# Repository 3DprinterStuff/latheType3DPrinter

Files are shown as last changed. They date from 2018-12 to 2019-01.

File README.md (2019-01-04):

# latheType3DPrinter

this is a dump of files related to mod to convert a standard 3D-Printer to a lathe type 3D-printer. A lathe type printer prints on rolls, as described in https://de.scribd.com/doc/147351838/Lathe-Type-3D-Printer. Printing on a bottle was shown at the 35C3 (assembly only).

# contact me

you can reach me by mail: printerstuff@riseup.net

# hardware

The basis for the modifaction is a ANET A8 printer. This printer was used, because i expected to destroy the hardware while experimenting (so this is no recomendation). Luckily the hardware still lives.

The main modification was to remove the heatbead and to replace it with a roll.

## removing the heatbed

The heatbed can be removed the basicaly doing the build process in reverse. The heatbed, the gliders and the rod holding the heatbed were removed. To not confuse the 3Dprinter, the heatbed was put next to the 3Dprinter with the wirering still attached. It may server as a tea warmer from now on.

## choose a roll

Choose a sturdy and round rod or pipe to print on. The usual rules for surfaces apply. For PLA i found that paper rolls and a steel pipe covered in masking tape worked well. Bottles are fun, but not easy to work with. This is because the fillament (PLA) doesn't stick well on cold metal/glass. Putting masking tape or smearing a layer of glue on the roll helps with the adhesion. 

The roll should be as round as possible. Bottles are actually not round and paper rolls are often ovals, too. For carpet rolls plastic parts exist that ensure roundness and have centered holes that can be usefull for mounting. For metal pipes ensure a clean cut so the pipe doesn't wobble later. A properly manufactured roll would probably best.

## mounting the roll

build some sort of contraption that holds the roll in place while rotating. The contraption must allow the bottle to rotate on the Y axis.

The rotational axis should be below the extruder to ensure the printing is happening on top of the bottle instead of on the side of the bottle. Printing a bit on the side of the roll causes little harm, but is bad style.

The rotational axis has to be parallel to the printers X axis. If the rotational axis is missalined printing quality will suffer or the print will fail, since the distance between the roll and the extruder won't be uniform. 

This can be validated by positioning the extruder ~ 1 mm above the roll and moving the Y/X Axis. If the distance to the roll stays uniform, the roll is mounted perfectly.

In this repo there are mountpoints that can be clicked into the case of an ANET A8 and multiple holders for different rolls. These holders are very custom (exept for the mate bottle one). The designs are very simple so you probably want to design your own. If you are printing

The bearings for the mounts in this repo are engines from old harddrives (HDD). Using standardised bearings would be the smarter thing probably, but costs hacker points.

## make the roll roll

Many 3D printers have the mechanics for X/Z Axis on top and the side of the printer and move the heatbead to have an Y Axis. The roll should replace the headbed and transform horizontal Y Axis movement with rotational Y Axis movement. This transformation happens by moving the upper part of a toothwheel instead of the heatbed. 

The toothwheel should be fitted onto the roll in a way it doesn't slip. In the best case it is easy to remove, centered and is tight enough to not rotate around the roll.

The orginal timing belt was cut and bolted onto the heatbed. A new and looped timing belt should be aquired and placed so it connects the Y Axis enigine with the upper side of the toothwheel. The timing belt should fit tight to reduce chances of skipping and to improve precision. In my case i used the wheel opposite of the Y Axis engine, but with some more distance than usual. 

The timing belt i used was from an old scanner so the dimension of your timing belt will likely differ. You should ensure it has roughly the needed length and take care it has the proper distance between the teeth. In my case it was 2 mm distance between the teeth. My guess is that for historical reasons any timing belts removed from old scanners will work.

## using the mechanics

With the modification done the 3D-printer should be ready to work. You can test the basic motion by doing the movement manually. If the printer doesn't fall apart and the roll stays centered below the extruder for multiple complete rotations, the mechanics should be fine.

One issue to resolve is how to handle the z-stopper. The usual position will probably way too low, so i removed it and press it manually when needed. As an unpleasent side effect is that the extruder will ram into the roll until the button is pressed or something. Since the button will never be pressed something will break so be carefull. This is especially bad, if the gcode for a print contains a HOME Z or HOME X/Y/Z for example at the start or the end of the print.

## homing the printer

The X-axis can be homed like without a modification. I prefer moving the X-axis to a point 1-2 cm left of the start of the roll and reset the printer. This is very dirty, but works for me. Feel free to solve this properly though.

The Y-Axis doesn't have to be homed at all, if the roll is has no special sides. Homing the Y-Axis will still result in the roll rotating till the y-stopper is pressed manually. This results in a fast rotation, but the roll and the rolls mount should be able to handle it.

I home the Z-Axis by moving the extruder above the roll and triggering the HOME-Z manually. The printer does a fast movent first where you should stop the extruder ~ 1 mm above the roll. Press the Z-stopper once to stop the extruder. Immediatly afterwards the printer will move the extruder up a bit and solwer it slowly again. Press the Z-stopper again to stop the extruder ~ 0.2 mm above the roll.

The printer should be homed now. I disabled/removed automatic homing in the gcode to prevent accidential destruction of the device. Also the printer should be prevented from moving throuh the holders for the roll when done with the printing.

## actually print something

You may print aribtrary 3D models that were sliced traditionally. Since the printers Firmware and slices behaves as the roll is a long flatbed it will print but will have of perspective skew. for some millimeter high the skew is negligeble for objects that are some centimeters high the skew will be obvious. The printer will also have a maximum value for the y coordiniate. This will have to be disabled or circumvented. In my printers case nagative Y coordinates were not capped and moving to -40000 mm Y was possible.

I prefered to write g-code generators in python. This allowed my to do what i actually want to do. While the sourcecode is in this repository it is very bad code and not abstracted properly.

An proper slicer or a more abstracted gcode generator is future work amound other things.

## what now ?

For the moment i'll glady help anybody to convert 3D printers to rotation based 3D printers. Also i welcome any energy put towards to having a slicer or an abstracted gcode generator for this type of printer. Please talk to me though, so we have the opportunity to coordinate.

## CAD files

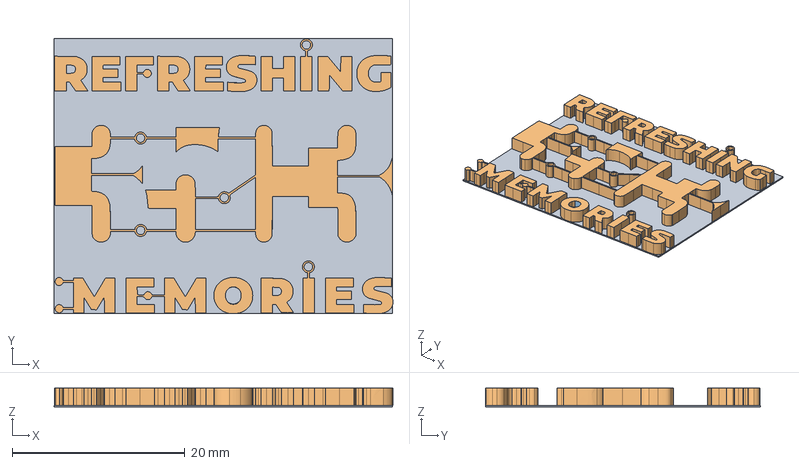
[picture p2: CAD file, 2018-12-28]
5Dprinter/35c3_logo_try6.fcstd
39.3 x 31.9 x 2.20 mm
Scale001
Pad001Body

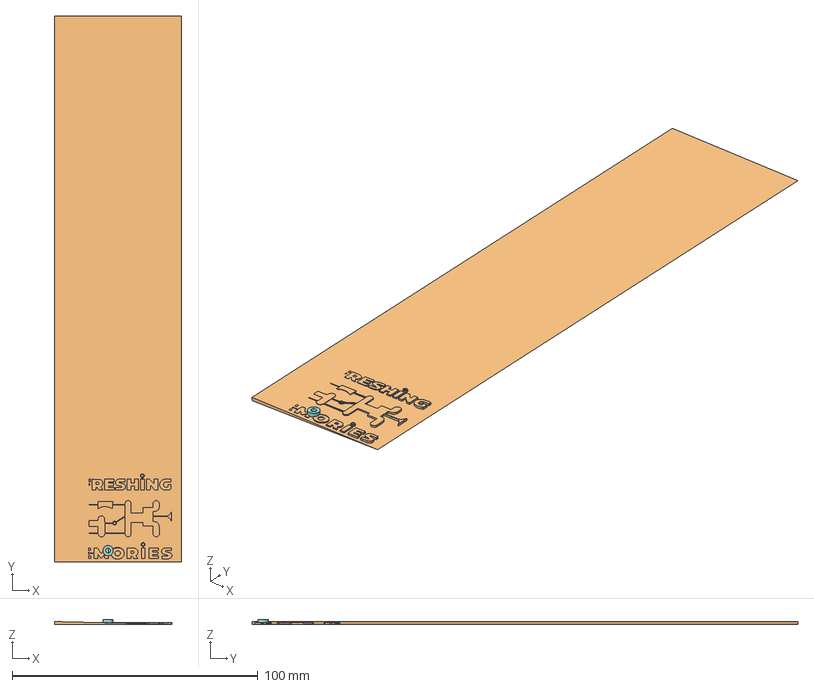
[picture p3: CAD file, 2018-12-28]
5Dprinter/bottle_print/logo_splited_5.fcstd
51.8 x 222.0 x 2.10 mm
Pad001Body
Scale004
PadBody
PocketBody
Pad001Body001
Pad002Body
Scale005

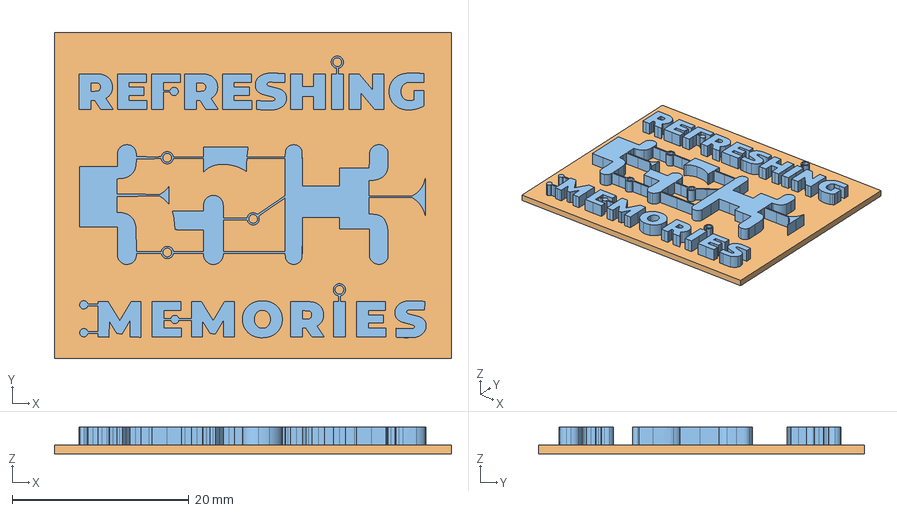
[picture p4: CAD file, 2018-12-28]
5Dprinter/35c3_logo_try3.fcstd
44.9 x 36.9 x 3.00 mm
Scale001

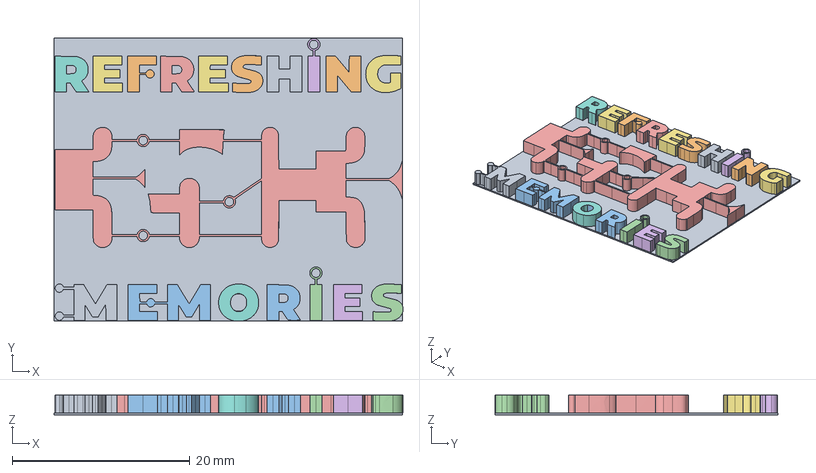
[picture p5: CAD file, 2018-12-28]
5Dprinter/35c3logo_6_2.stp
39.3 x 31.9 x 2.20 mm

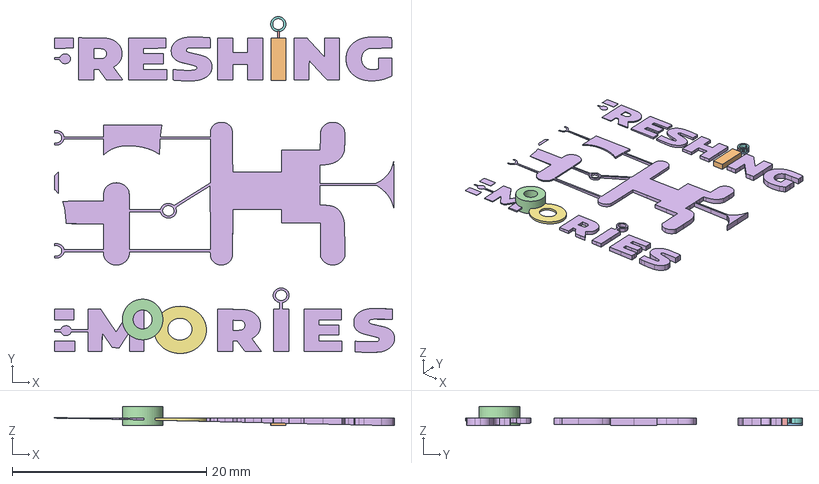
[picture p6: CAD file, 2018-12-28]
5Dprinter/bottle_print/logo_upper.fcstd
35.0 x 34.7 x 2.00 mm
Pad001Body
PadBody
PocketBody
Pad001Body001
Pad002Body

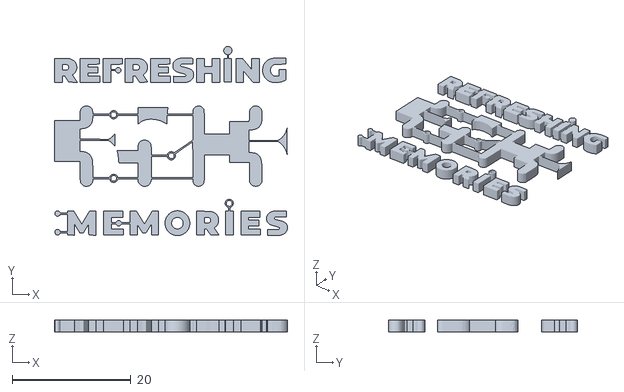
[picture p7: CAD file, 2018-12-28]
5Dprinter/35c3_logo1_txt.stl
39.2 x 31.8 x 2.00

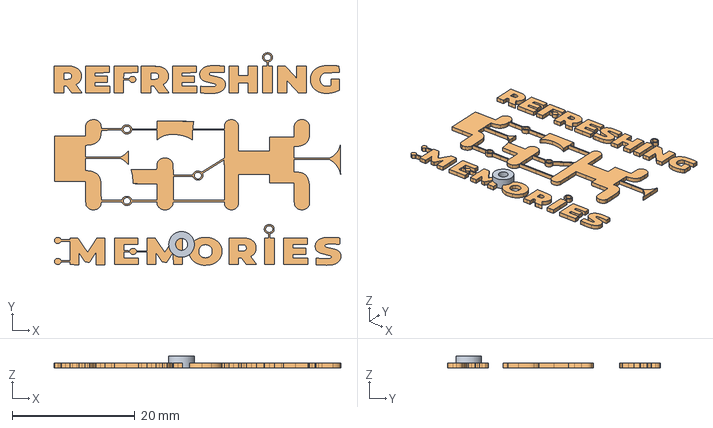
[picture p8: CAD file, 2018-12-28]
5Dprinter/bottle_print/logo_splited.fcstd
46.7 x 34.6 x 2.00 mm
Pad001Body
Scale004

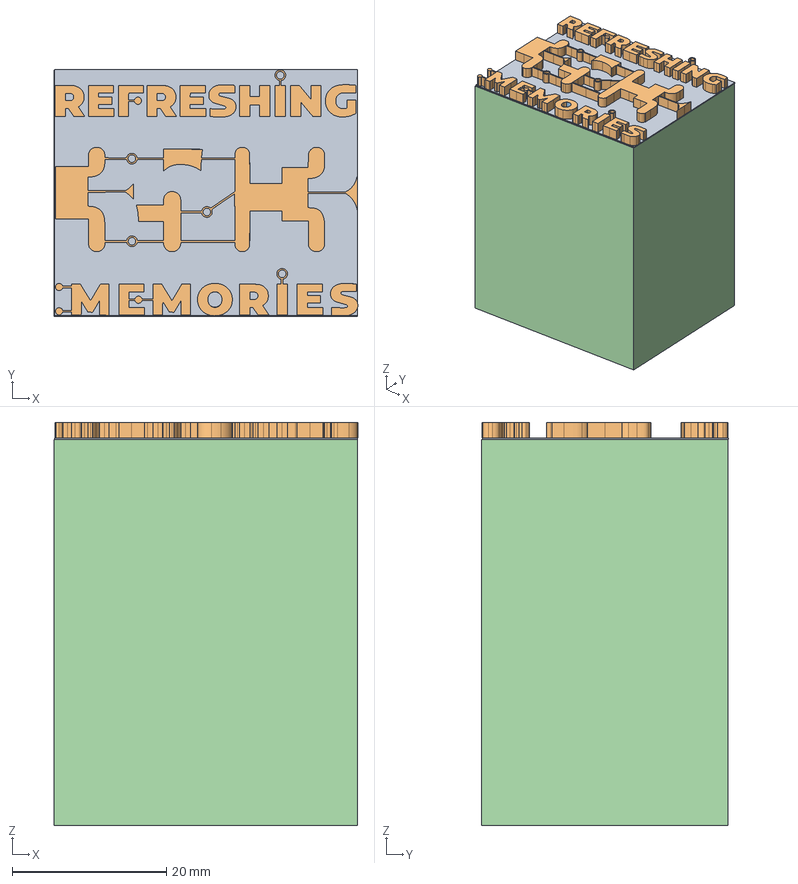
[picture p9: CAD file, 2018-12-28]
5Dprinter/35c3_logo_block.fcstd
39.3 x 32.0 x 52.2 mm
Scale001
Pad001Body

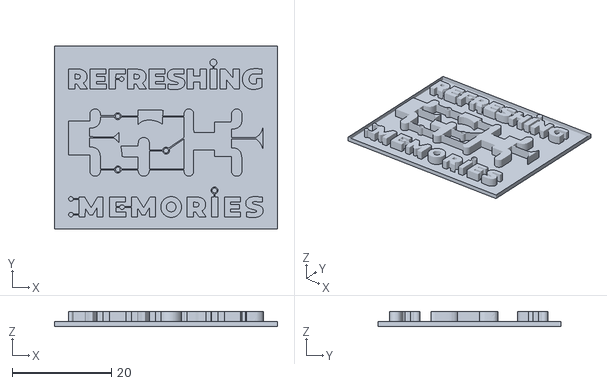
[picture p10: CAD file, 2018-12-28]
5Dprinter/35c3_logo1.stl
44.9 x 36.9 x 3.00

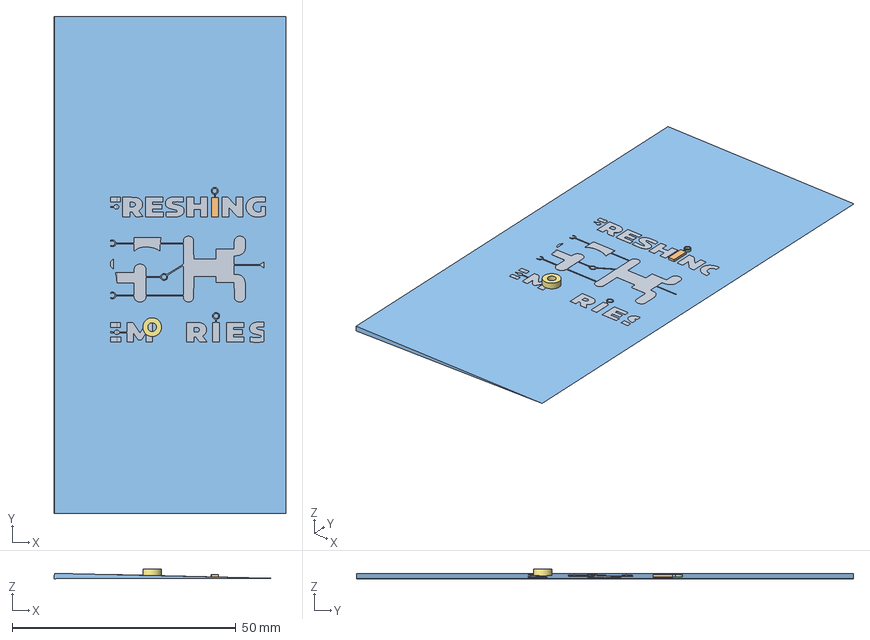
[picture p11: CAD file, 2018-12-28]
5Dprinter/bottle_print/logo_splited_6.fcstd
51.8 x 111.0 x 2.12 mm
Pad001Body
PadBody
PocketBody
Pad001Body001
Pad002Body

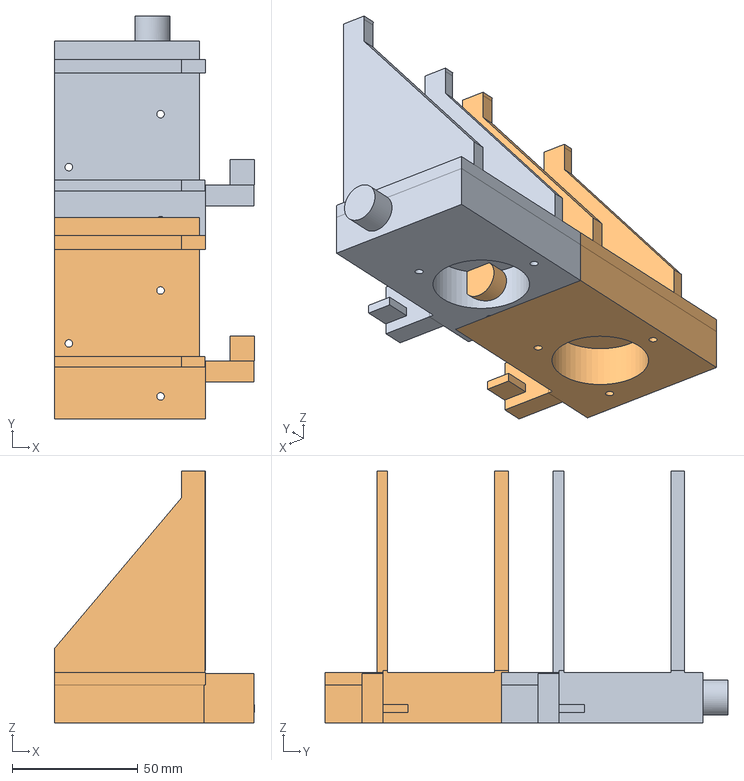
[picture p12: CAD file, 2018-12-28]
5Dprinter/holer_super_fancy.fcstd
79.5 x 160.0 x 100.0 mm

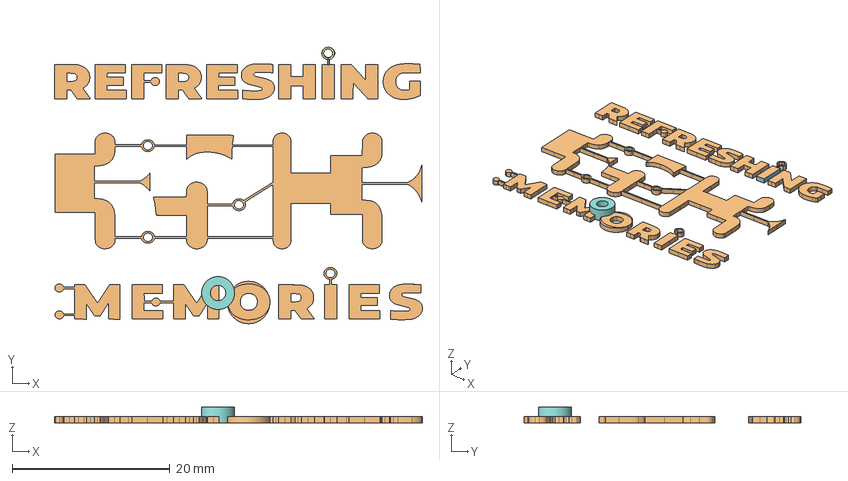
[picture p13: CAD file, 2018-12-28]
5Dprinter/bottle_print/logo_splited_4.fcstd
46.7 x 35.1 x 2.00 mm
Pad001Body
Scale004
PadBody
PocketBody
Pad001Body001
Pad002Body

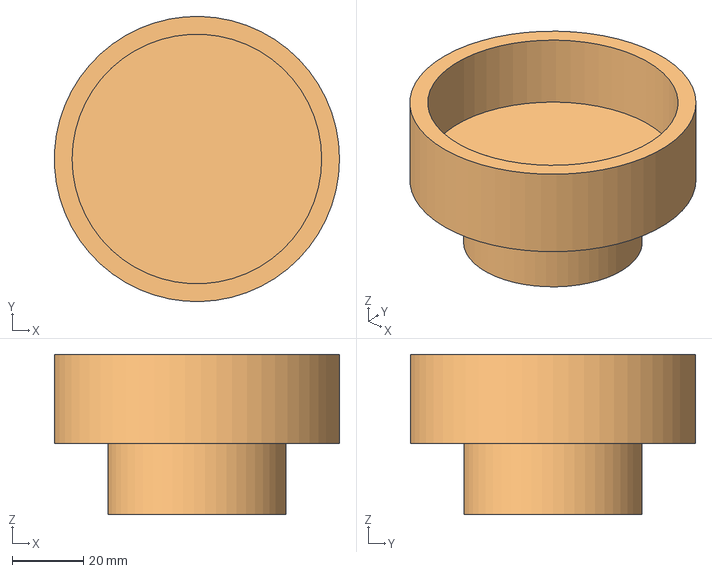
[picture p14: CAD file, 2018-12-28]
5Dprinter/holder7.fcstd
79.9 x 80.0 x 45.0 mm

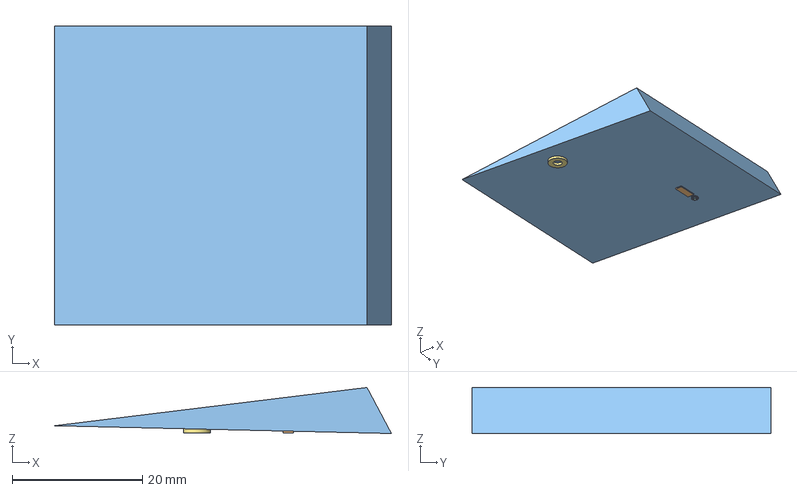
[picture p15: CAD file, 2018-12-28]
5Dprinter/bottle_print/logo_splited_7.fcstd
51.8 x 46.0 x 7.07 mm
Pad001Body
PadBody
PocketBody
Pad001Body001
Pad002Body

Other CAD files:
5Dprinter/bottle_print/logo_splited_3.fcstd
5Dprinter/bottle_print/logo_flat.fcstd
5Dprinter/bottle_print/logo_splited_2.fcstd
5Dprinter/holder4.fcstd
5Dprinter/35c3_logo6.stl
5Dprinter/35c3_logo6_2.stl
5Dprinter/35c3_logo_block.stl
5Dprinter/35c3_logo_try1.fcstd
5Dprinter/35c3_logo_try2.fcstd
5Dprinter/35c3_logo_try4.fcstd
5Dprinter/35c3_logo_try5?.fcstd
5Dprinter/35c3logo.stp
5Dprinter/35c3logo_6.stp
5Dprinter/bottle_print/logo.amf
5Dprinter/bottle_print/logo.fcstd
5Dprinter/bottle_print/logo.obj
5Dprinter/bottle_print/logo.stl
5Dprinter/bottle_print/logo_fixed.obj
5Dprinter/bottle_print/logo_lower.fcstd
5Dprinter/bottle_print/logo_lower.obj
5Dprinter/bottle_print/logo_lower.stl
5Dprinter/bottle_print/logo_upper.stl
5Dprinter/holder1.fcstd
5Dprinter/holder1.step
5Dprinter/holder1.stl
5Dprinter/holder2.fcstd
5Dprinter/holder2.stl
5Dprinter/holder3.fcstd
5Dprinter/holder3.stl
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
